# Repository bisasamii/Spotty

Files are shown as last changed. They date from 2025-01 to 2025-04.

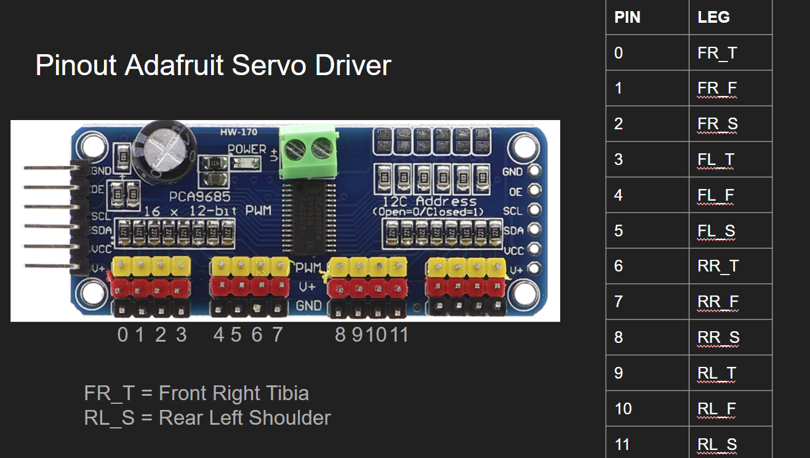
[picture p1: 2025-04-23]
Electronics/Wiring Diagrams/Servo Controller Pinout.png

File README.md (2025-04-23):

# Spotty
A quadruped Robot Dog based on the Boston Dynamics Spot
This repository contains all documentation, CAD files, electronic schematics.

<p align="center">
  Spotty Robot 1
  Spotty Robot 2
</p>

## Project Overview

Spotty is a four-legged (quadruped) open-source robot designed as a low-threshold learning platform for young talents interested in robotics and quantum technologies. The robot is constructed from PLA and can be extended with various modules, including a low-cost NV-based quantum sensor. The project aims to inspire curiosity and provide practical access to complex technologies.

Key features:
- Modular quadruped design inspired by Boston Dynamics' Spot
- Controlled by a Teensy 4.1 microcontroller with Adafruit PCA9685 for servo control
- 3D-printed components
- Integration of a basic NV-center quantum sensor (fluorescence-based magnetometer)
- Open-source hardware and software for educational purposes

## Repository Contents

- `/CAD`: 3D models (STL) for robot parts
- `/Electronics`: Schematics, wiring diagrams, and bill of materials
- `/Code`: Arduino/Teensy code for robot and remote
- `/Docs`: Detailed documentation

## Getting Started

1. Print the necessary parts using FDM 3D printing (recommended material: PLA).
2. Assemble the mechanical components and electronics following the guides in `/Docs`.
3. Upload the code from `/Code` to your MCUs.
4. Explore and extend Spotty!

## Requirements

- Electronics from bill of materials
- Basic tools for 3D printing and electronics assembly

## Acknowledgements

- Inspired by the SpotMicro Open Source Community

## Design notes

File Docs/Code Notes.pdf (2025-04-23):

## A couple of comments about the Code

1. Ensure that you have all libraries installed to run the code
2. If you have multiple SDA/SCL connected make sure to check the respective libraries for support. For example if you use the pins SDA1 and SCL1 you have to use “Wire1” in the arduino code. Not every library supports Wire1, Wire2,...
So you will have to make changes to the library to get everything to work

How the code is built:
The code has a main .ino file which is basically the main program. I have added multiple header files to make everything more clean:
- globals: Here are some global variables, constants an macros that you can change to your needs (for example servo settings, measurements,...)
- functions: Here are some functions for my mp3 module, NRF and compass module. Basically everything that is not related to servos or movement
- myBody: For the servos and movement of the robot I have decided to do a object oriented approach. The “MyBody” class controls the entire robot body, coordinates leg movements, selects the gait type, and regulates the walking behavior.
- myLeg: Declares the MyLeg class, which represents a single robot leg. It includes methods for stepping, position control, and updating the servos at the joints.
- myServoMotor: Declares the ServoMotor class, which encapsulates control of a servo motor, including motion interpolation, limits, correction factors, and direct actuation of the motor.

How the code generally works:
To understand how the code operates generally it is important to understand how the main .ino file operates. This picture can help you with this:

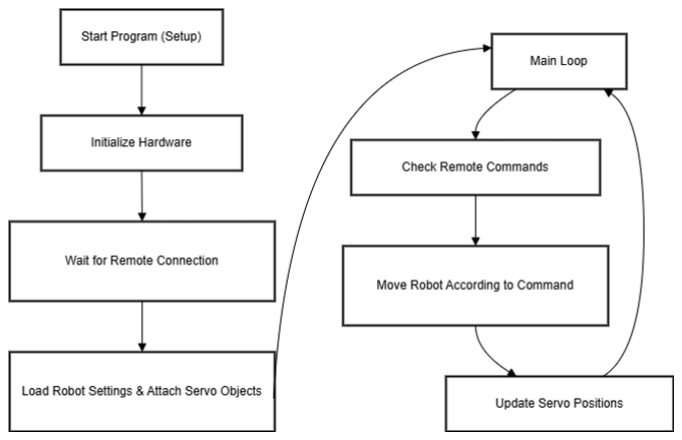
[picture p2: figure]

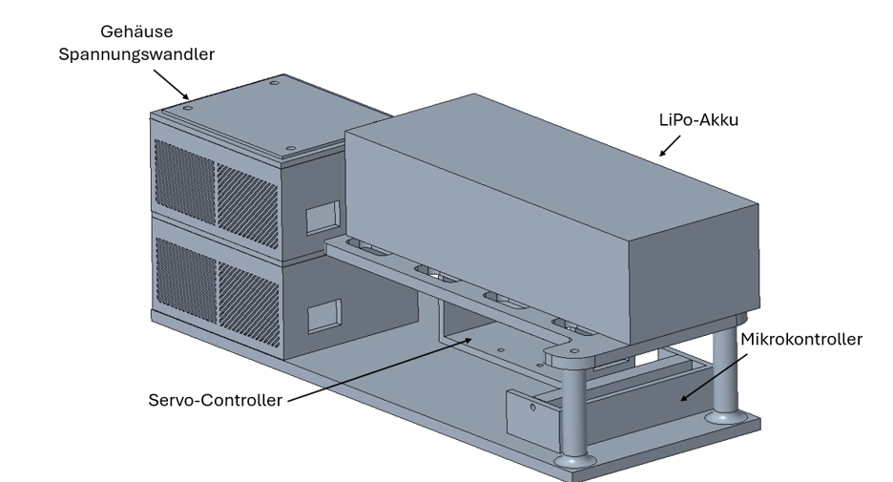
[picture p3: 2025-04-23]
Docs/Electronics Bracket.png

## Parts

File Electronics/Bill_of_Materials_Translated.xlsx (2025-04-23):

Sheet: Spotty
Name | Description | Quantity | Example Link
Motor (35kgcm) | Feetech FT6335 | 12 | https://www.premium-modellbau.de/feetech-ft6335-digital-metall-servo-67g-35kg-0-192sec-6v-8-4v-robotik-3600
Servo Controller | PCA9685 16 Channel 12 Bit PWM | 1 | https://www.amazon.de/AZDelivery-PCA9685-Servotreiber-Arduino-Raspberry/dp/B072N8G7Y9?hvadid=697141436093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
Microcontroller | Teensy 4.1 (much faster!) | 1 | https://www.amazon.de/Teensy-4-1-Mit-Stiftleisten/dp/B08CTM3279?__mk_de_DE=%C3%85M%C3%85%C5%BD%C3%95%C3%91
Servo Extensions | 3-pin Extension Cable for Servo Motors | 12 | https://www.amazon.de/Verl%C3%A4ngerungskabel%EF%BC%8CJR-Servoverl%C3%A4ngerung%EF%BC%8CServokabel%EF%BC%8CServokabel-Stecker-Verl%C3%A4ngerung%EF%BC%8C-sizes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
Step-Down Converter | 12 A output, converts battery voltage to 8.4V for servos | 1 | https://www.amazon.de/AZDelivery-Spannungsregler-Spannungswandler-Einstellbar-kompatibel/dp/B08T12J8KL
Step-Down Converter | Converts to Arduino logic voltage | 1 | https://www.amazon.de/Converter-Binghe-Spannungsregler-Einstellbares-Abw%C3%A4rtsmodul/dp/B0D7BWSTCX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
On/Off Power Switch | Must be suitable for high current | 1 | https://www.amazon.de/Demeras-Hochstrom-EIN-Aus-Schalter-RC-Flugzeugmodell-Schaltersteuerungssystem/dp/B08SLXX1J2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
Motor On/Off Switch | 12V | 1 | https://www.amazon.de/Kippschalter-Schalter-Wasserdicht-Wippschalter-Beleuchtet/dp/B0CQVKPJ39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
PowerTrain Cable, Red | For wiring before the voltage converter | 1 | https://www.amazon.de/Makerfire-Silikondraht-Elektrokabel-Kupfer-Hochtemperaturdraht-Flugzeugbatterien/dp/B09NFGJHYJ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
PowerTrain Cable, Black | For wiring before the voltage converter | 1
Low Voltage Cable | For logic boards (e.g., Arduino) | 1 | https://www.amazon.de/75mm%C2%B2Silikon-Elektronik-Elektrischer-RC-Flugzeuge-Haushaltsger%C3%A4te/dp/B09GKB582P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
DC Voltmeter Set | Monitor PowerTrain voltage | 1 | https://www.amazon.de/GTIWUNG-Spannungspr%C3%BCfer-Led-anzeige-Verpolungsschutz-Druckmessung/dp/B0BWLS9MVX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
Servo Tester | Calibrate the servos | 1 | https://www.amazon.de/diymore-Digital-Aluminiumgeh%C3%A4use-Multifunktions-Servocontroller/dp/B09Y94LLP6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
Battery Holder | For servo tester | 1 | https://www.amazon.de/VGOL-Batteriehalter-Empf%C3%A4ngergeh%C3%A4use-AA-Batterieeins%C3%A4tze-JST-Stecker/dp/B09QHRLMPX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
Servo Horn Set | Aluminium Buttons | 1 | https://www.amazon.de/DollaTek-Aluminium-Metall-H%C3%B6rner-Roboter/dp/B07F71J1Q2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
Screw & Nut Set | M2, M3, M4, M5 | 1 | https://www.amazon.de/Schrauben-Zylinderschrauben-Innensechskant-Unterlegscheiben-Gewindeschrauben/dp/B0CZNRW4MJ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
Bearing Set | 8165mm | 1 | https://www.amazon.de/ANGEEK-Kugellager-Metallkugellager-Doppelschild-Rillenkugellager/dp/B08Z8H3SV5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
Threaded Inserts Set | M2,M3,M4,M5 | 1 | https://www.amazon.de/ruthex-Gewindeeinsatz-Sortimentskasten-St%C3%BCck-Kunststoffteile/dp/B08K1BVGN9
Battery Pack | 14.8V 5000mAh | 1

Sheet: Remote
Name | Description | Quantity | Example Link
OLED 1 | Small Screen | 1 | https://www.amazon.de/MakerHawk-Anzeigemodul-Bildschirm-kompatibel-Mikrocontollern/dp/B07BDFXFRK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
OLED 2 | Large Screen | 1 | https://www.amazon.de/gp/product/B0CFFK32S8/ref=sw_img_1?smid=AE3E5WPQSSR6E&th=1
Joystick Module |  | 2 | https://www.amazon.de/gp/product/B077Z8QN3S/ref=sw_img_1?smid=A1XDN6LSMACAXM&psc=1
Trigger Switch |  | 4 | https://www.amazon.de/gp/product/B07VCCNVZP/ref=sw_img_1?smid=A8Q1GF4RT2D75&th=1
Sliding Potentiometer |  | 4 | https://www.amazon.de/gp/product/B07WSQPJ79/ref=sw_img_1?smid=AQ1IBDB6G2RRD&psc=1
Momentary Push Button | Mode Switch | 2 | https://www.amazon.de/gp/product/B0DFMMG1ZP/ref=sw_img_1?smid=A1GIQVBLUITC0P&th=1
LED | for indicator | 1 | https://www.amazon.de/gp/product/B088K8DVMQ/ref=sw_img_1?smid=A29559WHI6ZTR8&th=1
Battery + Charging Cable |  | 1 | https://www.amazon.de/gp/product/B08YJQDRSM/ref=sw_img_1?smid=A1CTK3ECWVKPGM&psc=1
3-Pole On/Off Switch |  | 1 | https://www.amazon.de/gp/product/B0CSCZGR68/ref=sw_img_1?smid=A1GIQVBLUITC0P&psc=1
3.3 V Regulator |  | 1 | https://www.amazon.de/gp/product/B07VGNPP7N/ref=sw_img_1?smid=A1X7QLRQH87QA3&th=1
5 V Regulator |  | 1 | https://www.amazon.de/gp/product/B07DJ5HZ7G/ref=sw_img_1?smid=A3SCFTIO8CSK1X&psc=1
NRF24 |  | 2

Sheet: Remote2
Name | Description | Quantity | Example Link
Joystick Module |  | 2 | https://www.amazon.de/gp/product/B077Z8QN3S/ref=sw_img_1?smid=A1XDN6LSMACAXM&psc=1
LED |  | 1
Battery + Charging Cable |  | 1 | https://www.amazon.de/gp/product/B08YJQDRSM/ref=sw_img_1?smid=A1CTK3ECWVKPGM&psc=1
5V Regulator |  | 1 | https://www.amazon.de/gp/product/B07DJ5HZ7G/ref=sw_img_1?smid=A3SCFTIO8CSK1X&psc=1
NRF24 |  | 2

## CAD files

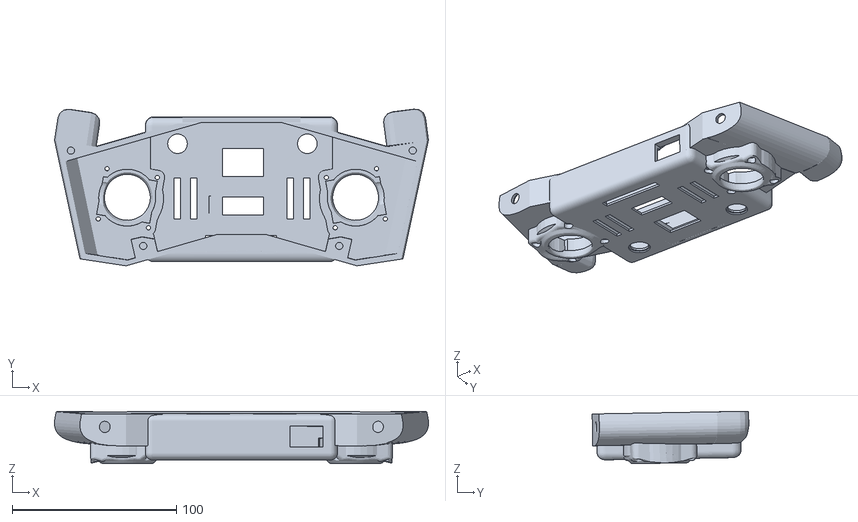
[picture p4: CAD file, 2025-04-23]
CAD/Remote/Cover_Front_V2.stl
227.6 x 95.3 x 31.9

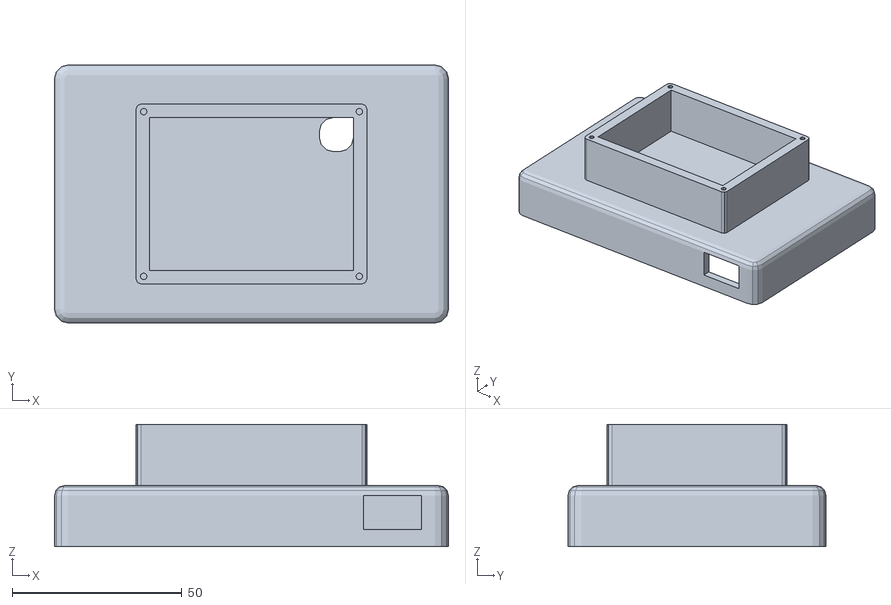
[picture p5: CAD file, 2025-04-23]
CAD/Remote2/Back.stl
116.0 x 76.0 x 36.0

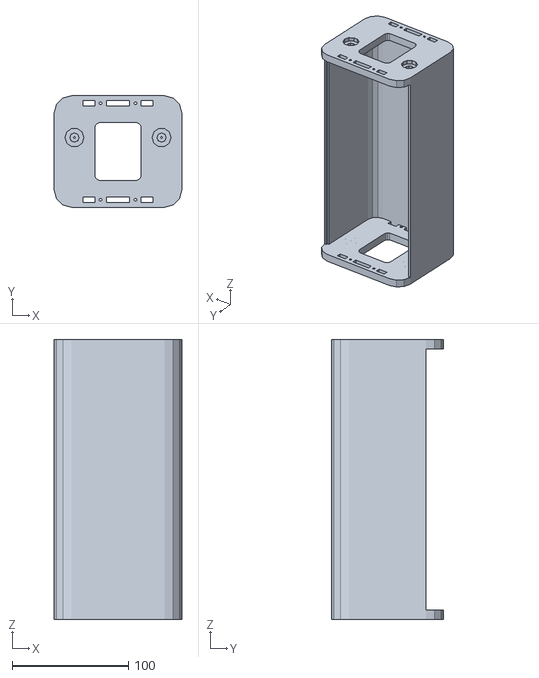
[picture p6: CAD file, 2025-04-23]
CAD/Spotty/Body/BODY_SPOTTY.stl
110.0 x 96.0 x 241.0

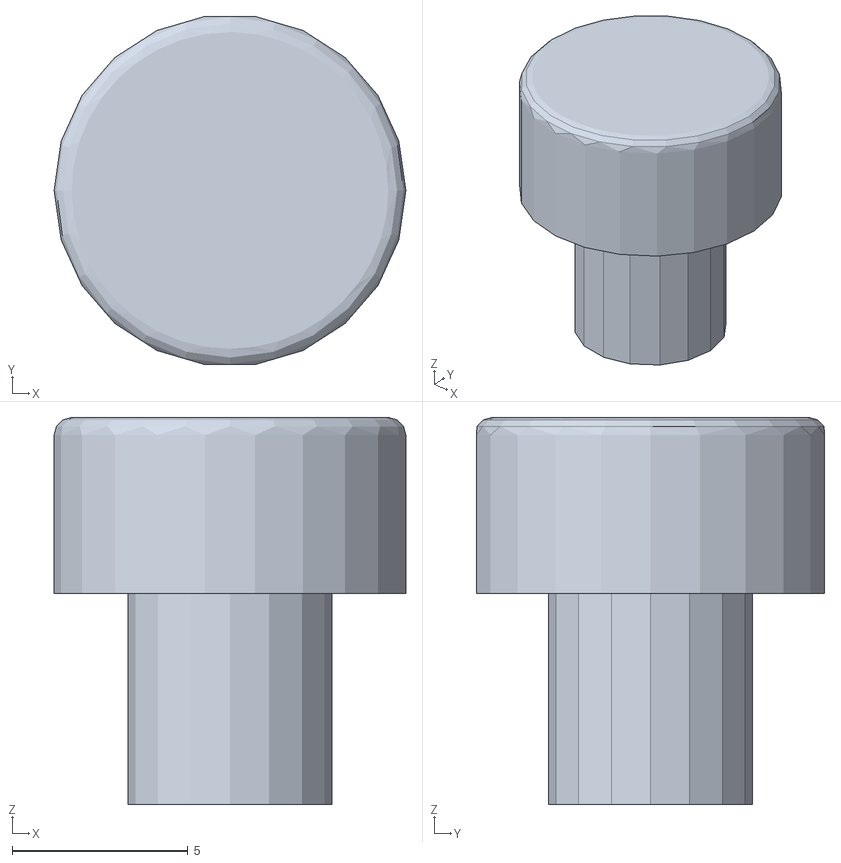
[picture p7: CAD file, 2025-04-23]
CAD/Spotty/Body/Lock/lock3.stl
10.0 x 9.90 x 11.0

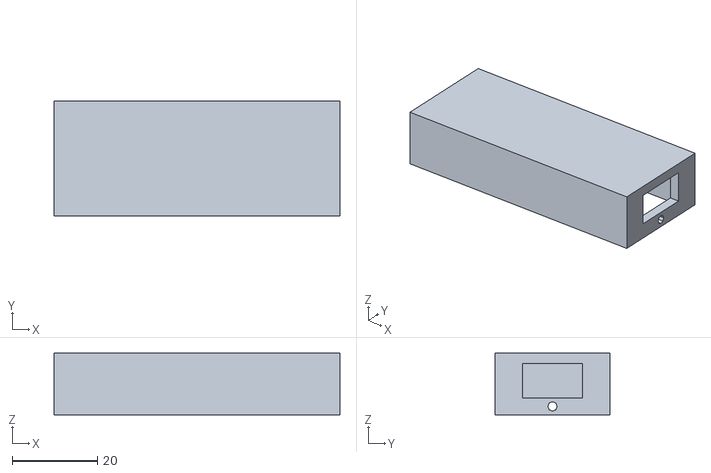
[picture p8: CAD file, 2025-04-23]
CAD/Spotty/Electronicsbracket/teensy_case.stl
67.0 x 27.0 x 14.5

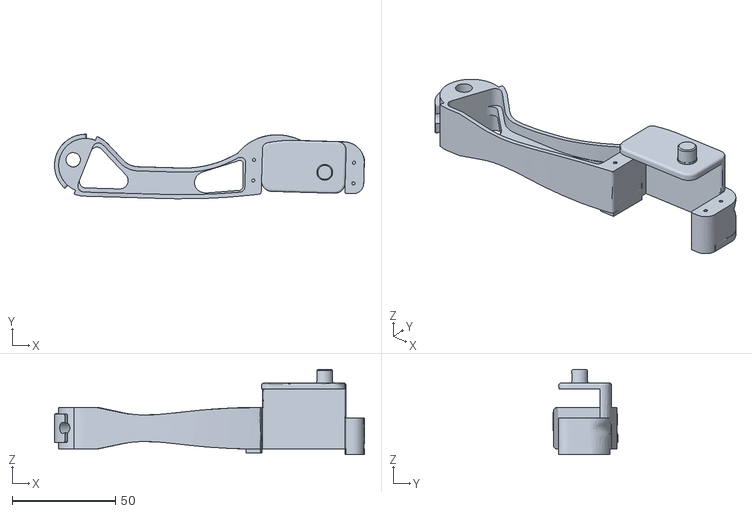
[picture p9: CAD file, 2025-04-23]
CAD/Spotty/Leg/TIBIA_RIGHT_SPOTTY.stl
150.2 x 31.3 x 41.2

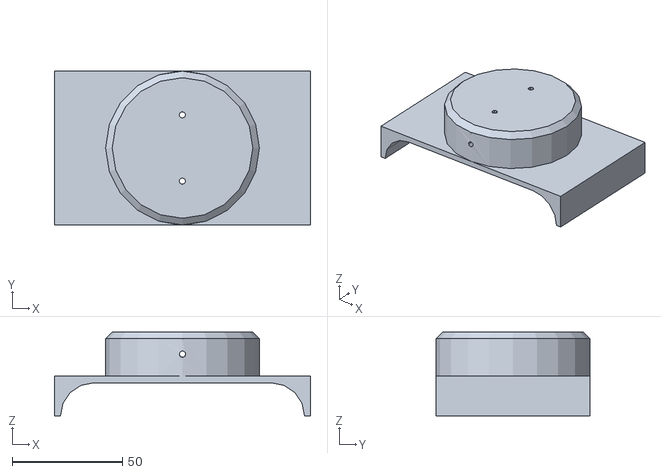
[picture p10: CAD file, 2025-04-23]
CAD/Spotty/Stand/aufnahme.stl
116.0 x 69.7 x 38.0

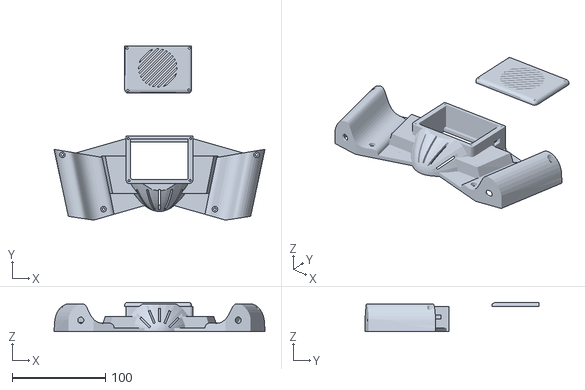
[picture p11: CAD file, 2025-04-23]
CAD/Remote/Cover_Back_V2.stl
225.8 x 186.5 x 31.1

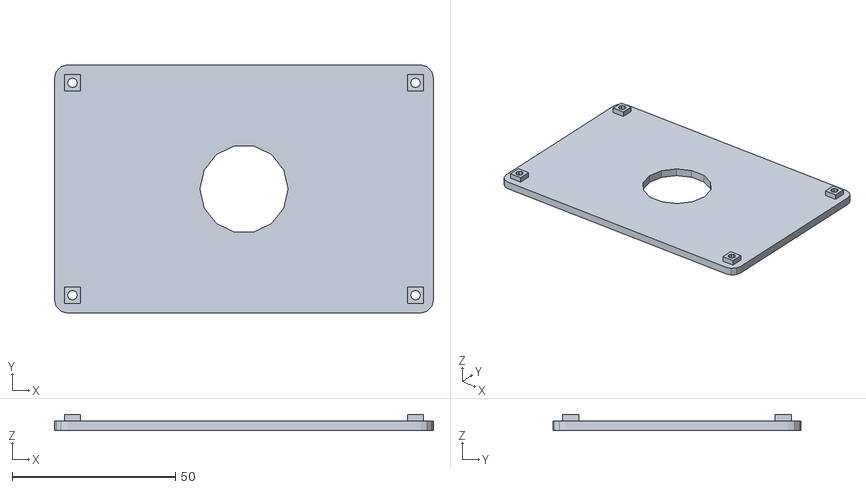
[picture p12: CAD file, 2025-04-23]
CAD/Remote2/Front.stl
116.0 x 76.0 x 5.00

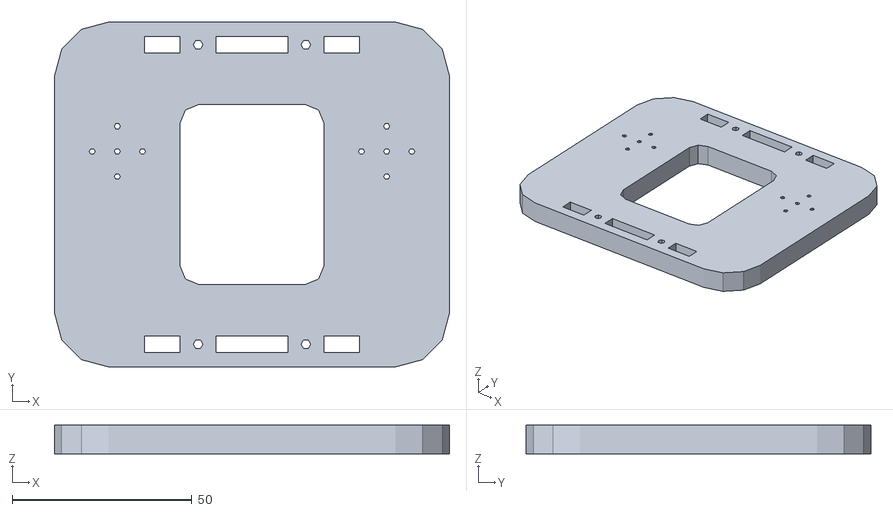
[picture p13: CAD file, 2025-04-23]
CAD/Spotty/Body/FACEPLATE2_SPOTTY.stl
110.0 x 96.0 x 8.00

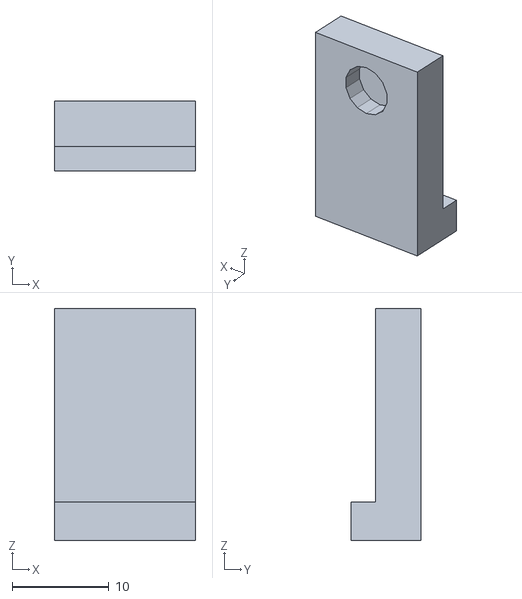
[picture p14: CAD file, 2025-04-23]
CAD/Spotty/Body/Lock/lock2.stl
14.6 x 7.20 x 24.0

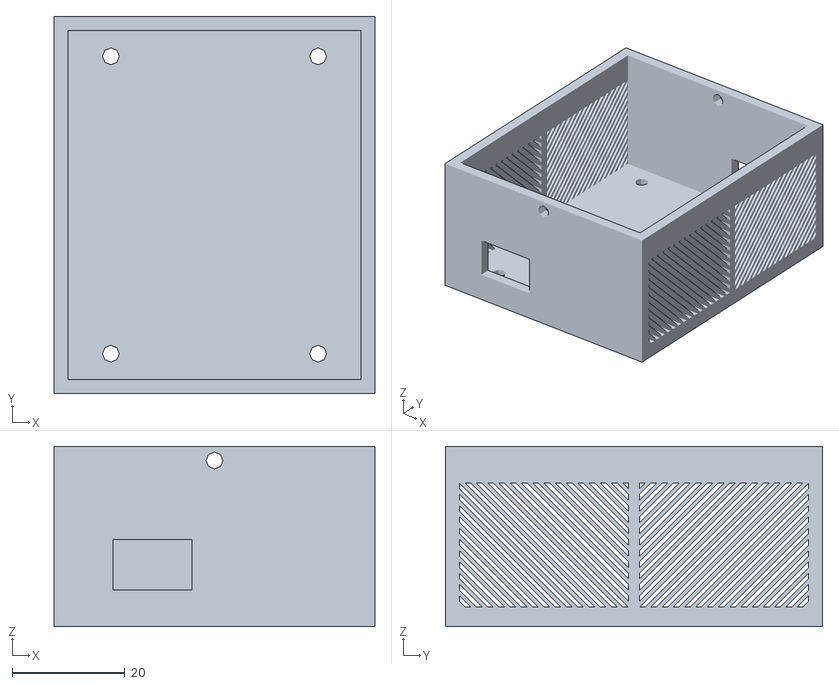
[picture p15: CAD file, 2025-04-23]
CAD/Spotty/Electronicsbracket/BUCK_CONVERTER_CASE.stl
57.0 x 67.0 x 32.0

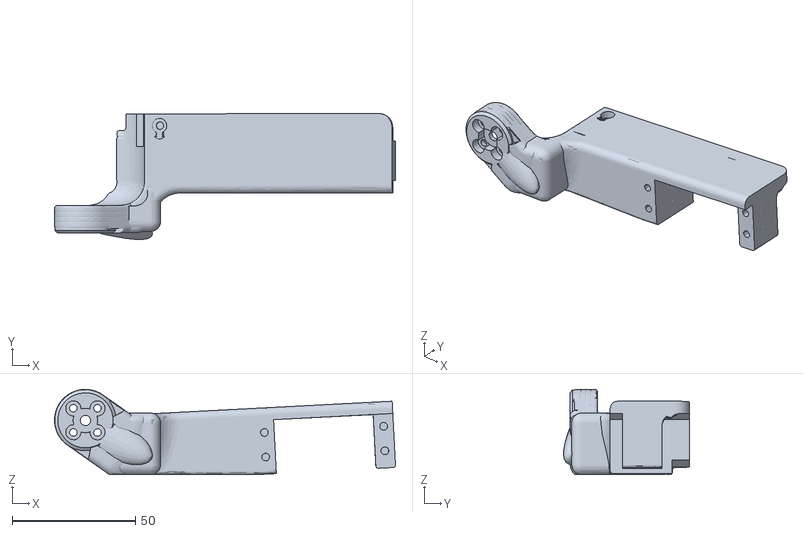
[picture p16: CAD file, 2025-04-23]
CAD/Spotty/Leg/FEMUR_RIGHT_SPOTTY.stl
138.5 x 51.2 x 34.7

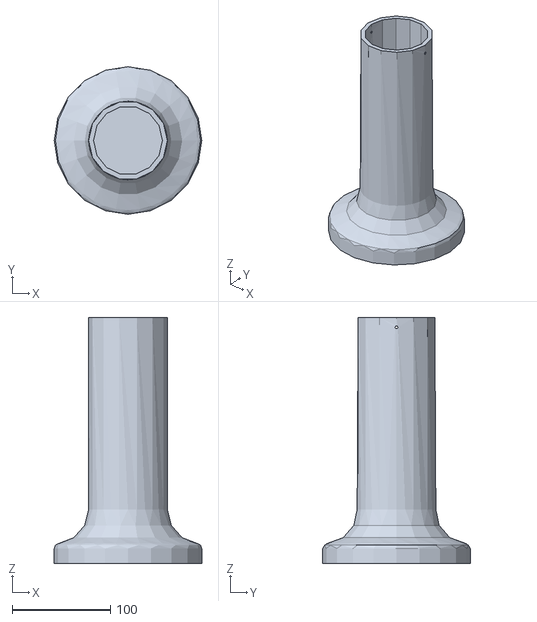
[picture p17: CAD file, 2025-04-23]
CAD/Spotty/Stand/base.stl
150.0 x 150.0 x 250.0

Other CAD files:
CAD/Remote2/Batterylid.stl
CAD/Spotty/Body/BODYLID_SPOTTY.stl
CAD/Spotty/Body/Lock/lock1.stl
CAD/Spotty/Electronicsbracket/servo_board_case.stl
CAD/Spotty/Body/CONNECTORBODY_SPOTTY.stl
CAD/Spotty/Body/FACEPLATE_SPOTTY.stl
CAD/Spotty/Electronicsbracket/baseplate.stl
CAD/Spotty/Electronicsbracket/buck_converter_lid.stl
CAD/Spotty/Electronicsbracket/teensy_lid.stl
CAD/Spotty/Electronicsbracket/upper_plate.stl
CAD/Spotty/Leg/BRACE_SPOTTY.stl
CAD/Spotty/Leg/COAX_RIGHT_SPOTTY.stl
CAD/Spotty/Leg/FEMURCOVER_RIGHT_SPOTTY.stl

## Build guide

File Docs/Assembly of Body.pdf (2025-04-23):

## Assembly of the Body

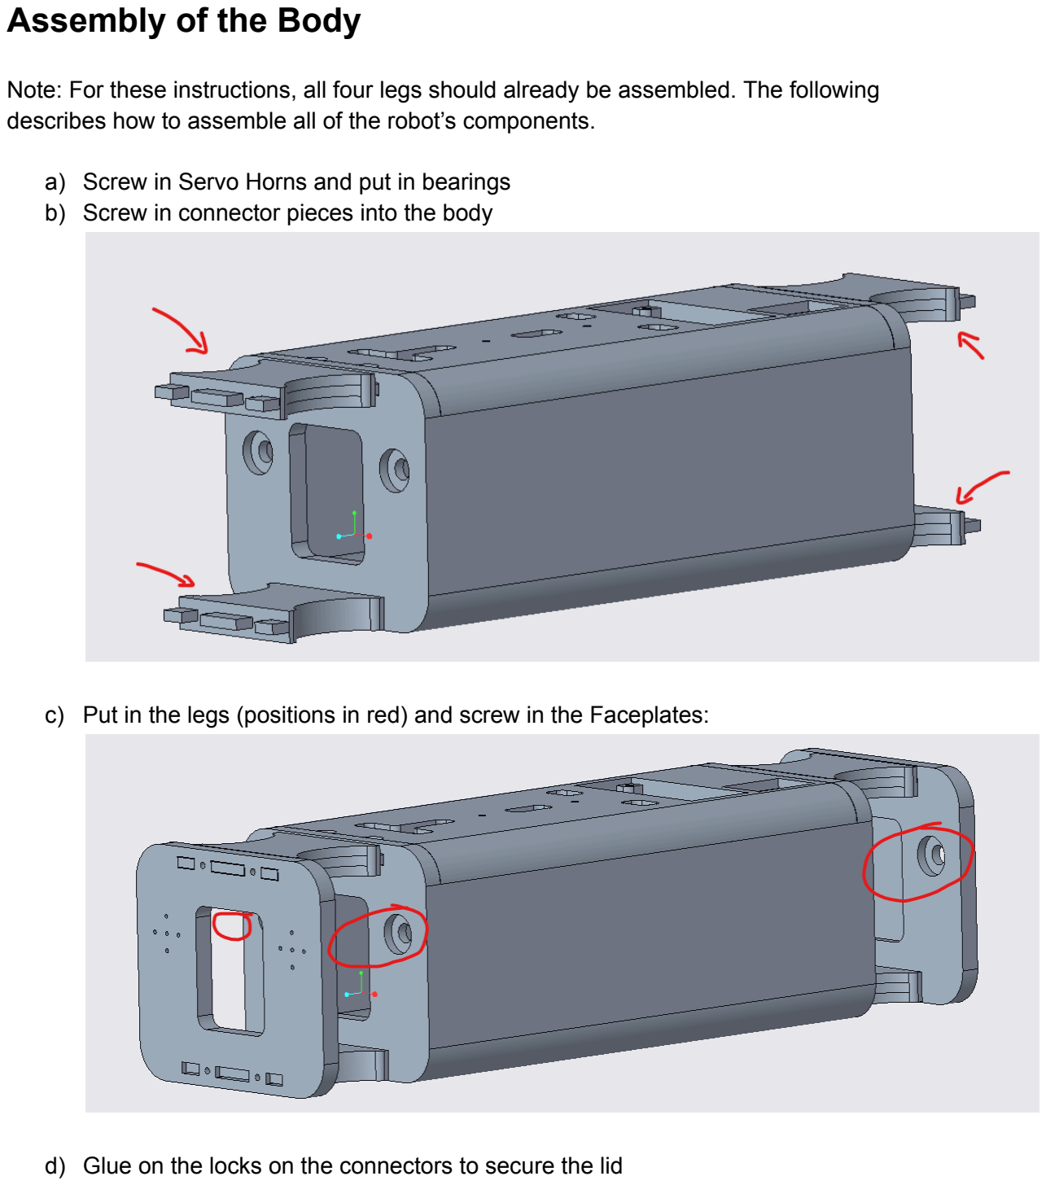
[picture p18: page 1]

Note: For these instructions, all four legs should already be assembled. The following describes how to assemble all of the robot’s components.

a) Screw in Servo Horns and put in bearings
b) Screw in connector pieces into the body
c) Put in the legs (positions in red) and screw in the Faceplates:
d) Glue on the locks on the connectors to secure the lid

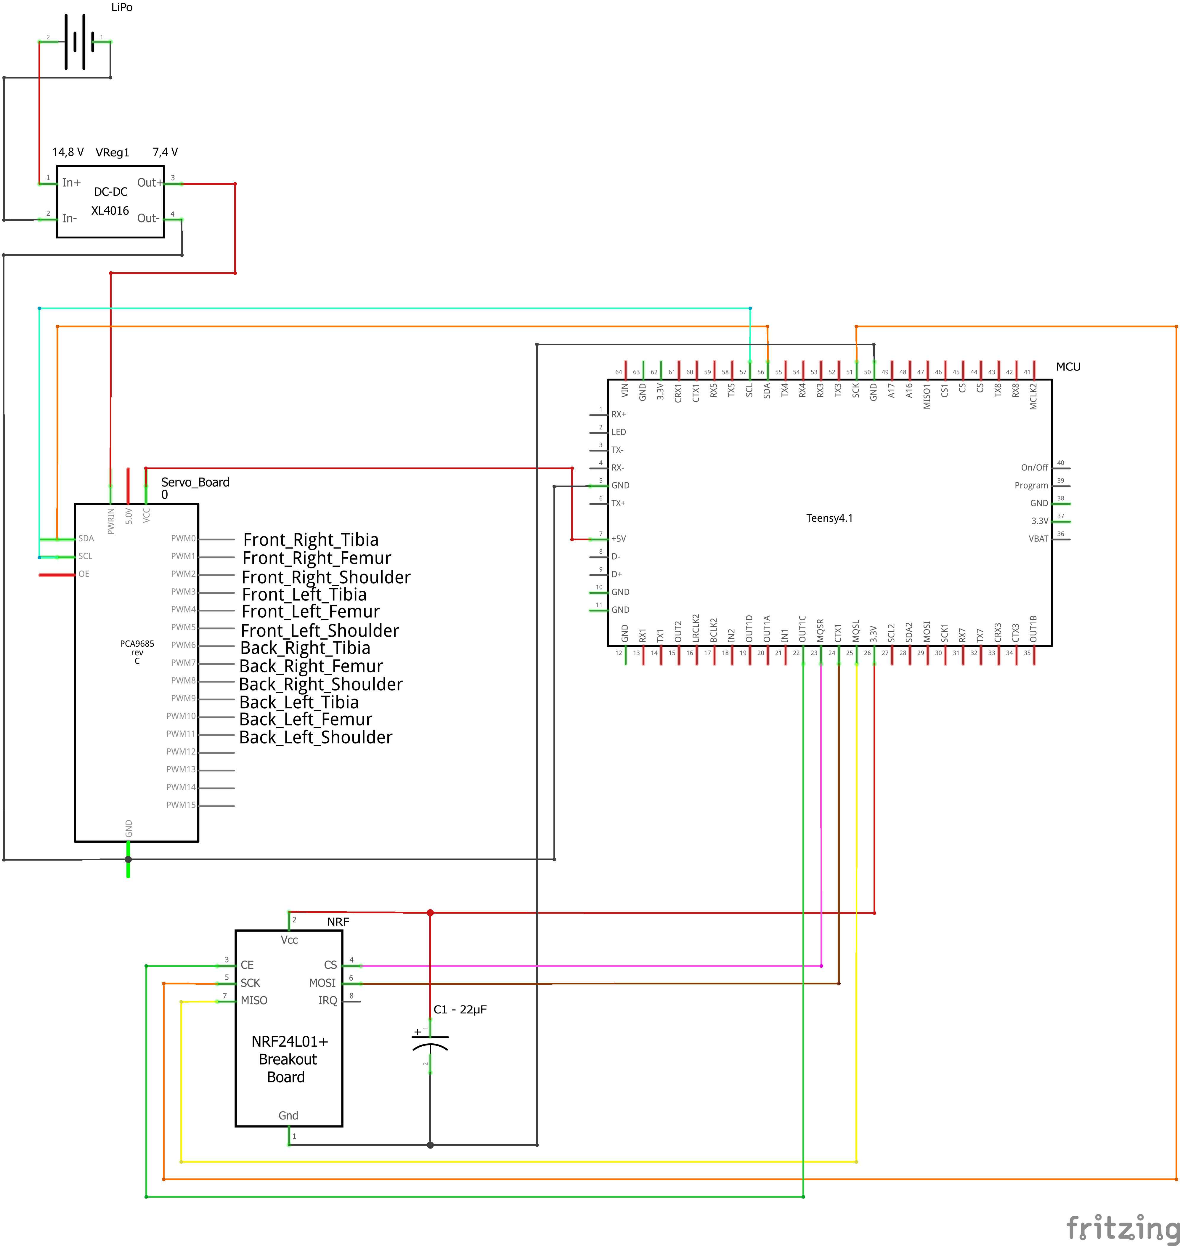
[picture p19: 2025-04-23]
Electronics/Wiring Diagrams/Spotty_Wiring.png

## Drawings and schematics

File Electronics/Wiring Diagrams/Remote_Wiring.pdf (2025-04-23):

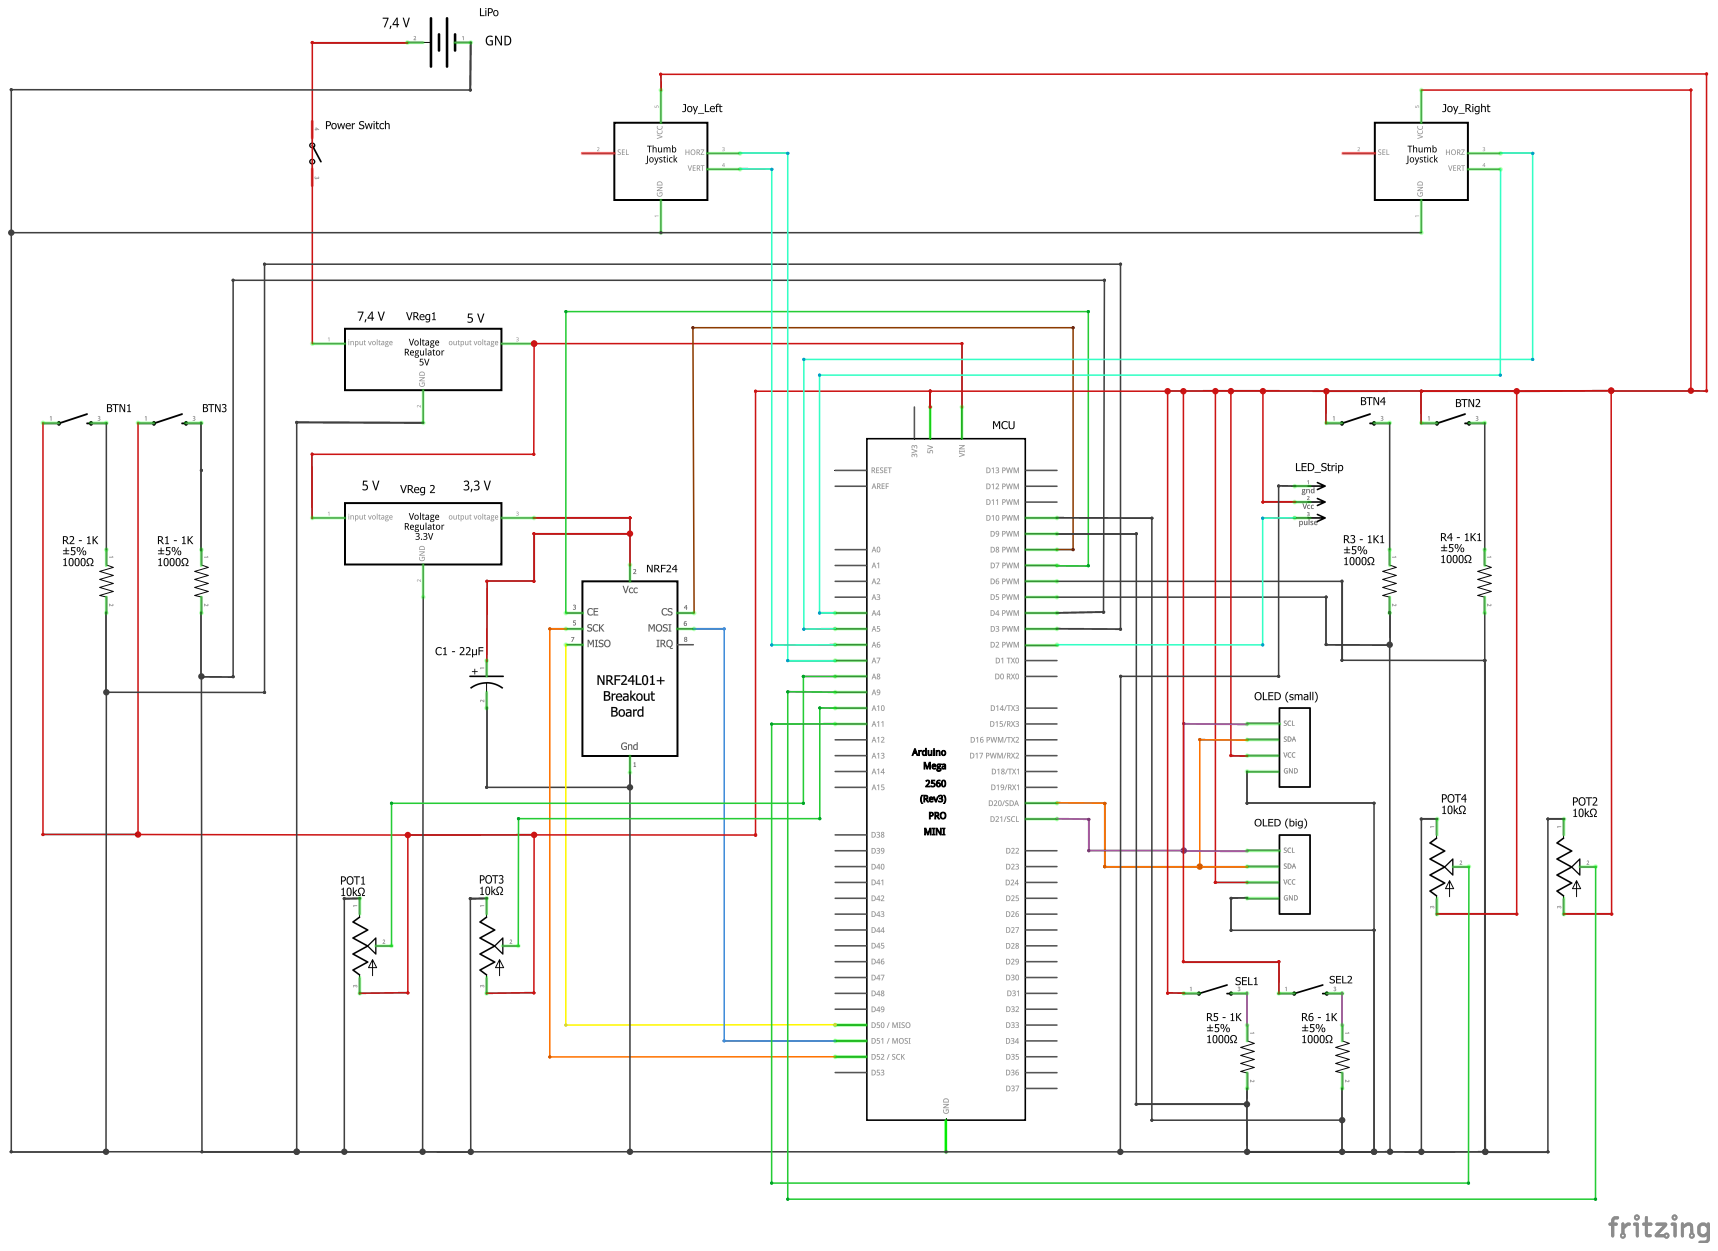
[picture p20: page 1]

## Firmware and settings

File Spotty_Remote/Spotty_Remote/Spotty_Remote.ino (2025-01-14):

#include "globals.h"

//========================================
//  NRF24 Pin Wiring for Arduino Mega/Nano:
//  pin 7/7 -> CE pin
//  pin 8/8 -> CSN pin
//  pin 52/13 -> SCK pin
//  pin 51/11 -> MOSI pin
//  pin 50/12 -> MISO pin
//  pin xx -> IRQ pin (unused)
//========================================
//function prototypes
void fade(int redStartValue, int redEndValue, int greenStartValue, int greenEndValue, int blueStartValue, int blueEndValue, int totalSteps, int fadeBack, int rgbNum = 99);
void blink_rgb_num(int rgb_val[3], int rgb_val2[3], int rgbNum=99);


void setup() {
  Serial.begin(19200);
  while (!Serial) {
  }

  delay(3000);
  if (nrf_active) {
    if (!radio.begin()) {
      if (debug2) Serial.println(F("radio hardware is not responding!!"));
      while (1) {}
    } else {
      if (debug2) Serial.println(F("radio hardware is ready!"));
      radio.setPALevel(RF24_PA_LOW);
      radio.setPayloadSize(sizeof(tm_data));
      radio.setChannel(124);
      radio.openWritingPipe(address);
      radio.enableAckPayload();
      radio.setRetries(5,5); // delay, count

      if (debug2) Serial.println(F("radio ready to transmit"));
    }
  }

  pinMode(POT1_PIN, INPUT);
  pinMode(POT2_PIN, INPUT);
  pinMode(POT3_PIN, INPUT);
  pinMode(POT4_PIN, INPUT);

  pinMode(LJX_PIN, INPUT);
  pinMode(LJY_PIN, INPUT);

  pinMode(RJX_PIN, INPUT);
  pinMode(RJY_PIN, INPUT);

  led_strip.begin();
  led_strip.setBrightness(rgb_bright);
  wipe_strip();

  pinMode(BTN1_PIN, INPUT_PULLUP);
  pinMode(BTN2_PIN, INPUT_PULLUP);
  pinMode(BTN3_PIN, INPUT_PULLUP);
  pinMode(BTN4_PIN, INPUT_PULLUP);

  pinMode(SEL1_PIN, INPUT_PULLUP);
  pinMode(SEL2_PIN, INPUT_PULLUP);
  
  // initialize with the I2C addr
  display.begin(SSD1306_SWITCHCAPVCC, OLED_ADDR);  
  display2.begin(SSD1306_SWITCHCAPVCC, OLED_ADDR2);  

  rgb_check(8);
  
  display.clearDisplay();
  display.setTextSize(1);
  display.setTextColor(WHITE);
  display.setCursor(0,0);
  display.println("Initializing...");
  display.display();
    
  display2.clearDisplay();
  display2.setTextSize(1);
  display2.setTextColor(WHITE);
  display2.setCursor(10,0);
  display2.println("Initializing...");
  display2.display();
  
  delay(2000);
  display.clearDisplay();
  display2.clearDisplay();
  display2.setTextSize(2);
  
  //animate bitmap
  display.drawBitmap(-10, 5,  smbmp, 128, 64, WHITE);
  display.display();
  display.startscrollright(0x00, 0x07);

  //strobe version banner
  for (int i=25;i>0;i--) {
    int d = (i*4);
    if (i > 22) d = (i*10);
    if (i == 25) d = (i*100);
    display2.setCursor(22, 2);
    display2.setTextSize(2);
    display2.println("SPOTTY");
    display2.setCursor(16, 18);
    display2.print("REMOTE");
    display2.setCursor(86, 22);
    display2.setTextSize(1);
    display2.print(" v");
    display2.println(VERSION);
    display2.display();
    delay(d);
    display2.clearDisplay();
    display2.display();
    if (i == 25) d = (i*10);
    delay(d);
  }
  display2.clearDisplay();
  display2.display();
  delay(2000);

  display2.setCursor(30,12);
  display2.setTextSize(3);
  display2.print("READY!");
  display2.display();

  display.stopscroll();
  display.clearDisplay();
  display.display();

  //init remote with Nova
  if (nrf_active) {
    for (int i = 0; i < data_num; i++) {
      tm_data[i] = 0;
    }
    tm_resp = nrf_check();
  }

  if (debug) Serial.println(F("Ready!"));
  pattern = 10;
  pattern_cnt = 16;
  pattern_int = 150;
}

void loop() {
  if (millis() - controlsUpdate > controlsInterval) {
    check_pots();
    check_buttons();
    check_joysticks();
    check_mode();
  }

  if (nrf_active && (millis() - lastNRFUpdate > nrfInterval)) tm_resp = nrf_check();

  if (millis() - lastRGBUpdate > rgbInterval) rgb_check(pattern);
  if (millis() - lastOLEDUpdate > oledInterval) oled_refresh();
  if (millis() - lastOLED2Update > oled2Interval) oled2_refresh();
  if (millis() - lastDisplayUpdate > displayInterval) update_display(2);

  if (batt_active && (millis() - lastBatteryUpdate > batteryInterval)) battery_check(0); 
  if (activity_active && millis() - inactivityUpdate > inactivityInterval) inactivity_check(); 

  if (debug3) {

    Serial.print("pot1:");
    Serial.print(p1);
    Serial.print("\tpot2:");
    Serial.print(p2);
    Serial.print("\tpot3:");
    Serial.print(p3);
    Serial.print("\tpot4:");
    Serial.print(p4);
  
    if (!plotter) {
      Serial.print("\tbtn1:");
      Serial.print(b1);
      Serial.print("\tbtn2:");
      Serial.print(b2);
      Serial.print("\tbtn3:");
      Serial.print(b3);
      Serial.print("\tbtn4:");
      Serial.print(b4);
  
      Serial.print("\tsel1:");
      Serial.print(s1);
      Serial.print("\tsel2:");
      Serial.print(s2);
      Serial.print("\tsel3:");
      Serial.print(s3);
    }
  
    Serial.print("\trjx:");
    Serial.print(analogRead(RJX_PIN));
    Serial.print("\trjy:");
    Serial.print(analogRead(RJY_PIN));
  
    Serial.print("\tljx:");
    Serial.print(analogRead(LJX_PIN));
    Serial.print("\tljy:");
    Serial.println(analogRead(LJY_PIN));
    delay(50);
  }

}

bool nrf_check() {
  bool resp = false;

  if (tm_data) {
    resp = radio.write(&tm_data, sizeof(tm_data));
    if (resp) {
      if (radio.isAckPayloadAvailable()) {
        radio.read(&rc_data, sizeof(rc_data));
        if (debug2) {
          for (int i = 0; i < data_num; i++) {
            Serial.print(rc_data[i]);Serial.print("\t");
          }
          Serial.println(" ACK REC");
        }
      }

      if (debug2) {
        for (int i = 0; i < data_num; i++) {
          Serial.print(tm_data[i]);Serial.print("\t");
        }
        Serial.println(" DATA SENT");
      }
    } else {
      //handle failed transmission
      if (debug2) {
        Serial.print(F("Transmission failed! "));
        Serial.println(" ");
      }
    }

    lastNRFUpdate = millis();
  }

  return resp;
}

void inactivity_check() {
  if (inactivity_set) {
    inactivity_cnt++;
    if (debug) {
      Serial.print(F("icnt: "));
      Serial.println(inactivity_cnt);
    }

    //put into sleep mode
    if (inactivity_cnt == inactivity_loop) {
      if (debug) {
        Serial.println(F("update display"));
      }
      update_display(4);
    } else if (inactivity_cnt == (inactivity_loop * 2)) {
      inactivity_cnt = 0;
      display.clearDisplay();
      display2.clearDisplay();
    }
  } else {
    inactivity_cnt = 0;
  }
  inactivity_set = 1;
  inactivityUpdate = millis();
}

void check_pots() {
  int updis = 0;
  if (debug4) {
    pot_max = 128;    //adjust max to OLED pixel width for debug mode
  }

  int p1c = analogRead(POT1_PIN);
  if (p1c != p1p) {
    //double-check jumpy pots
    if (p1c == analogRead(POT1_PIN)) {
      p1 = map(p1c, 0, 1023, pot_max, pot_min);
      if (p1 > pot_slack) {
        if (p1c > (p1p + pot_slack) || p1c < (p1p - pot_slack)) {
          inactivity_set = 0;
        }
        p1p = p1c;
        tm_data[6] = p1;
  
        if (debug4) {
          bdrawline(2,1,1,128,1);
          wdrawline(2,1,1,p1,1);
    
          cur_rgb_val1[0] = 125; cur_rgb_val1[1] = 0; cur_rgb_val1[2] = 125;
          cur_rgb_val2[0] = 0; cur_rgb_val2[1] = 125; cur_rgb_val2[2] = 125;
          rgb_num = 0;
          if (p1 > 100) {
            rgb_num = 4;
          } else if (p1 > 75) {
            rgb_num = 3;
          } else if (p1 > 50) {
            rgb_num = 2;
          } else if (p1 > 25) {
            rgb_num = 1;
          }
          pattern = 9;
          pattern_cnt = 1;
          pattern_int = 10;
        } else {
          per1 = map(p1, pot_max, pot_min, 100, -100); // convert reading to a percentage
          if (per1 < 3 && per1 > -3) per1 = 0;
          if (per1 != pper1) {
            pper1 = per1;
            updis = 1;
          }
        }
      }
    }
  }

  int p2c = analogRead(POT2_PIN);
  if (p2c != p2p) {
    //double-check jumpy pots
    if (p2c == analogRead(POT2_PIN)) {
      p2 = map(p2c, 0, 1023, pot_max, pot_min);
      if (p2 > pot_slack) {
        if (p2c > (p2p + pot_slack) || p2c < (p2p - pot_slack)) {
          inactivity_set = 0;
        }
        p2p = p2c;
        tm_data[7] = p2;
  
        if (debug4) {
          bdrawline(2,1,5,128,5);
          wdrawline(2,1,5,p2,5);
    
          cur_rgb_val1[0] = 255; cur_rgb_val1[1] = 0; cur_rgb_val1[2] = 55;
          cur_rgb_val2[0] = 55; cur_rgb_val2[1] = 0; cur_rgb_val2[2] = 255;
          rgb_num = 0;
          if (p2 > 100) {
            rgb_num = 4;
          } else if (p2 > 75) {
            rgb_num = 3;
          } else if (p2 > 50) {
            rgb_num = 2;
          } else if (p2 > 25) {
            rgb_num = 1;
          }
          pattern = 9;
          pattern_cnt = 1;
          pattern_int = 10;    
        } else {
          per2 = map(p2, pot_max, pot_min, 100, -100); // convert reading to a percentage
          if (per2 < 3 && per2 > -3) per2 = 0;
          if (per2 != pper2) {
            pper2 = per2;
            updis = 1;
          }
        }
      }
    }
  }

  int p3c = analogRead(POT3_PIN);
  if (p3c != p3p) {
    //double-check jumpy pots
    if (p3c == analogRead(POT3_PIN)) {
      p3 = map(p3c, 0, 1023, pot_max, pot_min);
      if (p3 > pot_slack) {
        if (p3c > (p3p + pot_slack) || p3c < (p3p - pot_slack)) {
          inactivity_set = 0;
        }
        p3p = p3c;
        tm_data[8] = p3;
  
        if (debug4) {
          bdrawline(2,1,26,128,26);
          wdrawline(2,1,26,p3,26);
    
          cur_rgb_val1[0] = 55; cur_rgb_val1[1] = 255; cur_rgb_val1[2] = 55;
          cur_rgb_val2[0] = 55; cur_rgb_val2[1] = 55; cur_rgb_val2[2] = 255;
          rgb_num = 0;
          if (p3 > 100) {
            rgb_num = 4;
          } else if (p3 > 75) {
            rgb_num = 3;
          } else if (p3 > 50) {
            rgb_num = 2;
          } else if (p3 > 25) {
            rgb_num = 1;
          }
          pattern = 9;
          pattern_cnt = 1;
          pattern_int = 10;
        } else {
          per3 = map(p3, pot_max, pot_min, 100, -100); // convert reading to a percentage
          if (per3 < 3 && per3 > -3) per3 = 0;
          if (per3 != pper3) {
            pper3 = per3;
            updis = 1;
          }
        }
      }
    }
  }

  int p4c = analogRead(POT4_PIN);
  if (p4c != p4p) {
    //double-check jumpy pots
    if (p4c == analogRead(POT4_PIN)) {
      p4 = map(p4c, 0, 1023, pot_max, pot_min);
      if (p4 > pot_slack) {
        if (p4c > (p4p + pot_slack) || p4c < (p4p - pot_slack)) {
          inactivity_set = 0;
        }
        p4p = p4c;
        tm_data[9] = p4;
  
        if (debug4) {
          bdrawline(2,1,31,128,31);
          wdrawline(2,1,31,p4,31);
    
          cur_rgb_val1[0] = 255; cur_rgb_val1[1] = 55; cur_rgb_val1[2] = 55;
          cur_rgb_val2[0] = 255; cur_rgb_val2[1] = 55; cur_rgb_val2[2] = 255;
          rgb_num = 0;
          if (p4 > 100) {
            rgb_num = 4;
          } else if (p4 > 75) {
            rgb_num = 3;
          } else if (p4 > 50) {
            rgb_num = 2;
          } else if (p4 > 25) {
            rgb_num = 1;
          }
          pattern = 9;
          pattern_cnt = 1;
          pattern_int = 10;
        } else {
          per4 = map(p4, pot_max, pot_min, 100, -100); // convert reading to a percentage
          if (per4 < 3 && per4 > -3) per4 = 0;
          if (per4 != pper4) {
            pper4 = per4;
            updis = 1;
          }
        }
      }
    }
  }

//  if (updis) update_display(1);
}

void check_buttons() {
  int b1c = digitalRead(BTN1_PIN);
  if (b1c != b1p) {
    b1 = b1c;
    b1p = b1c;
    inactivity_set = 0;
    tm_data[0] = b1;

    if (b1) {
      led_strip.setPixelColor(0, led_strip.Color(125, 125, 0));
    } else {
      led_strip.setPixelColor(0, led_strip.Color(0, 0, 0));
    }
    led_strip.show();
    if (debug4) {
      if (b1) {
        wfillcircle(2,40,20,5);
      } else {
        bfillcircle(2,40,20,5);
      }
    }
  }

  int b2c = digitalRead(BTN2_PIN);
  if (b2c != b2p) {
    b2 = b2c;
    b2p = b2c;
    inactivity_set = 0;
    tm_data[1] = b2;

    if (b2) {
      led_strip.setPixelColor(4, led_strip.Color(125, 125, 0));
    } else {
      led_strip.setPixelColor(4, led_strip.Color(0, 0, 0));
    }
    led_strip.show();
    if (debug4) {
      if (b2) {
        wfillcircle(2,88,20,5);
      } else {
        bfillcircle(2,88,20,5);
      }
    }
  }

  int b3c = digitalRead(BTN3_PIN);
  if (b3c != b3p) {
    b3 = b3c;
    b3p = b3c;
    inactivity_set = 0;
    tm_data[2] = b3;

    if (b3) {
      led_strip.setPixelColor(1, led_strip.Color(125, 125, 0));
    } else {
      led_strip.setPixelColor(1, led_strip.Color(0, 0, 0));
    }
    led_strip.show();
    if (debug4) {
      if (b3) {
        wfillcircle(2,30,10,5);
      } else {
        bfillcircle(2,30,10,5);
      }
    }
  }

  int b4c = digitalRead(BTN4_PIN);
  if (b4c != b4p) {
    b4 = b4c;
    b4p = b4c;
    inactivity_set = 0;
    tm_data[3] = b4;

    if (b4) {
      led_strip.setPixelColor(3, led_strip.Color(125, 125, 0));
    } else {
      led_strip.setPixelColor(3, led_strip.Color(0, 0, 0));
    }
    led_strip.show();
    if (debug4) {
      if (b4) {
        wfillcircle(2,98,10,5);
      } else {
        bfillcircle(2,98,10,5);
      }
    }
  }


  int s1c = digitalRead(SEL1_PIN);
  if (s1c != s1p) {
    s1 = s1c;
    s1p = s1c;
    inactivity_set = 0;
    tm_data[4] = s1;

    if (debug4) {
      if (s1) {
        wfillcircle(2,32,15,10);
        led_strip.setPixelColor(2, led_strip.Color(0, 255, 0));
      } else {
        bfillcircle(2,32,15,10);
        led_strip.setPixelColor(2, led_strip.Color(0, 0, 0));
      }
      led_strip.show();
    } else {
      if (s1 == LOW) {
      // Cycle through modes: 1 -> 2 -> 3 -> 4 -> 1 -> ...
      mode_index++;
      if (mode_index > 4) {
        mode_index = 1;
      }

      cur_rgb_val1[0] = 0; cur_rgb_val1[1] = 255; cur_rgb_val1[2] = 0;
      cur_rgb_val2[0] = 0; cur_rgb_val2[1] = 0; cur_rgb_val2[2] = 0;
      rgb_num = 99;
      pattern = 9;
      pattern_cnt = 1;
      pattern_int = 10;
      update_display(3);
    }
    }
  }

  int s2c = digitalRead(SEL2_PIN);
  if (s2c != s2p) {
    s2 = s2c;
    s2p = s2c;
    inactivity_set = 0;
    tm_data[5] = s2;

    if (debug4) {
      if (s2) {
        wfillcircle(2,96,15,10);
        led_strip.setPixelColor(2, led_strip.Color(255, 0, 0));
      } else {
        bfillcircle(2,96,15,10);
        led_strip.setPixelColor(2, led_strip.Color(0, 0, 0));
      }
      led_strip.show();
    } else {
      
      if (s2 == LOW) {
      selected_mode = mode_index;
      display2.clearDisplay();
      display2.setCursor(0, 0);
      display2.setTextSize(2);
      switch (mode_index) {
        case 1:
          display2.print("Walk");
          break;
        case 2:
          display2.print("Freestyle");
          break;
        case 3:
          display2.print("Trot");
          break;
        case 4:
        display2.print("Options");
        break;
      }
      display2.setCursor(0, 20);
      display2.setTextSize(1);
      display2.print("SELECTED!");
      display2.display();
      cur_rgb_val1[0] = 255; cur_rgb_val1[1] = 0; cur_rgb_val1[2] = 0;
      cur_rgb_val2[0] = 0; cur_rgb_val2[1] = 0; cur_rgb_val2[2] = 0;
      rgb_num = 99;
      pattern = 9;
      pattern_cnt = 1;
      pattern_int = 10;
      }
    }
  }
}


void check_joysticks() {
  byte rjxcen = 127;
  byte rjycen = 127;
  byte ljxcen = 127;
  byte ljycen = 127;

  int rjx = map(analogRead(RJX_PIN), rj_min, rj_max, j_min, j_max);
  if (rjx != tm_data[12]) {
    if (rjx < jstick_center[1] && rjx > -jstick_center[1]) {
      rjx = 0;
    }
    //    inactivity_set = 0;
    tm_data[12] = rjx;

    if (debug4) {
      if (!rjx && (!set_led[1] || !set_led[3])) {
        led_strip.setPixelColor(1, led_strip.Color(0, 0, 0));
        led_strip.setPixelColor(3, led_strip.Color(0, 0, 0));
        set_led[1] = 0;
        set_led[3] = 0;
      } else if (rjx > jstick_center[0]) {
        set_led[3] = 1;
        led_strip.setPixelColor(3, led_strip.Color(0, 0, 255));
      } else if (rjx < -jstick_center[0]) {
        set_led[1] = 1;
        led_strip.setPixelColor(1, led_strip.Color(0, 0, 255));
      }
    }
  }

  int ljx = map(analogRead(LJX_PIN), lj_min, lj_max, j_min, j_max);
  if (ljx != tm_data[10]) {
    if (ljx < jstick_center[1] && ljx > -jstick_center[1]) {
      ljx = 0;
    }
//    inactivity_set = 0;
    tm_data[10] = ljx;

    if (debug4) {
      if (!ljx && (!set_led[1] || !set_led[3])) {
        led_strip.setPixelColor(1, led_strip.Color(0, 0, 0));
        led_strip.setPixelColor(3, led_strip.Color(0, 0, 0));
        set_led[1] = 0;
        set_led[3] = 0;
      } else if (ljx > jstick_center[0]) {
        set_led[3] = 1;
        led_strip.setPixelColor(3, led_strip.Color(0, 0, 255));
      } else if (ljx < -jstick_center[0]) {
        set_led[1] = 1;
        led_strip.setPixelColor(1, led_strip.Color(0, 0, 255));
      }
      led_strip.show();
    }
  }

  int rjy = map(analogRead(RJY_PIN), rj_min, rj_max, j_max, j_min);
  if (rjy != tm_data[13]) {
    if (rjy < jstick_center[1] && rjy > -jstick_center[1]) {
      rjy = 0;
    }
//    inactivity_set = 0;
    tm_data[13] = rjy;

    if (debug4) {
      if (!rjy && (!set_led[0] || !set_led[4])) {
        led_strip.setPixelColor(0, led_strip.Color(0, 0, 0));
        led_strip.setPixelColor(4, led_strip.Color(0, 0, 0));
        set_led[0] = 0;
        set_led[4] = 0;
      } else if (rjy > jstick_center[1]) {
        set_led[0] = 1;
        led_strip.setPixelColor(0, led_strip.Color(0, 255, 0));
      } else if (rjy < -jstick_center[1]) {
        set_led[4] = 1;
        led_strip.setPixelColor(4, led_strip.Color(0, 255, 0));
      }
    }
  }

  int ljy = map(analogRead(LJY_PIN), lj_min, lj_max, j_max, j_min);
  if (ljy != tm_data[11]) {
    if (ljy < jstick_center[1] && ljy > -jstick_center[1]) {
      ljy = 0;
    }
//    inactivity_set = 0;
    tm_data[11] = ljy;

    if (debug4) {
      if (!ljy && (!set_led[0] || !set_led[4])) {
        led_strip.setPixelColor(0, led_strip.Color(0, 0, 0));
        led_strip.setPixelColor(4, led_strip.Color(0, 0, 0));
        set_led[0] = 0;
        set_led[4] = 0;
      } else if (ljy > jstick_center[1]) {
        set_led[0] = 1;
        led_strip.setPixelColor(0, led_strip.Color(0, 255, 0));
      } else if (ljy < -jstick_center[1]) {
        set_led[4] = 1;
        led_strip.setPixelColor(4, led_strip.Color(0, 255, 0));
      }
      led_strip.show();
    }
  }

  controlsUpdate = millis();

  if (debug4) {
    display.clearDisplay();
    display.setTextSize(2);
    display.setCursor(10,18);
    display.print(ljx);
    display.print(",");
    display.println(ljy);
    display.setCursor(10,47);
    display.print(rjx);
    display.print(",");
    display.println(rjy);
  }
}

void check_mode(){
  tm_data[14] = selected_mode;
}

/*
   -------------------------------------------------------
   OLED Functions
   -------------------------------------------------------
*/
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

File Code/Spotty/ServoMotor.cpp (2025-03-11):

#include <string.h>
#include "ServoMotor.h"
#include "globals.h"

ServoMotor::ServoMotor()
{
	mId = -1;
	mTargetDegree = -1;
	mCurrentDegree = -1;
	mIsMoving = false;
  mReverse = false;
  mName = NULL;
}

ServoMotor::~ServoMotor()
{
  if (mName)
    delete []mName;
}

void ServoMotor::update(unsigned long mills)
{
  if (mId < 0)
    return;

	if (mIsMoving)
	{
		if (mills >= mEndTime) //End of movement is reached: Write the target angle to the motor and set moving variable to false
		{

			write_degree(mTargetDegree);
			mIsMoving = false;
		}
		else //Time is smaller than end time which means that the movement is still performing
		{
      if (mTargetDegree == mCurrentDegree) //If Target is reached return
        return;
    
      double perc = (double)(mills - mStartTime) / (double)(mEndTime - mStartTime);

		  double pos_degree;

      if (mRamp > 0.0)
      {
				double velocitymax = (mTargetDegree - mStartDegree) / (1.0 - mRamp);

				double velocity;

        if (perc < mRamp) // ramp UP
				{
					velocity = perc / mRamp *  velocitymax;

					pos_degree = mStartDegree + perc * velocity / 2.0;

				}
				else if (perc < (1.0 - mRamp)) // constant velocity
				{
					velocity = velocitymax;

					pos_degree = mStartDegree + (mRamp / 2.0 + perc - mRamp) * velocitymax;

				}
				else // ramp DOWN
				{
					velocity = (1.0 - perc) / mRamp * velocitymax;

					pos_degree = mStartDegree + (1.0 - mRamp) * velocitymax - velocity * (1.0 - perc) / 2;

				}
      }
      else // No ramp
      {
		    pos_degree = mStartDegree + (mTargetDegree - mStartDegree) * perc;
        
      }
			write_degree(pos_degree);
		}
	}
}

void ServoMotor::write_degree(double degree)
{
	  if (mId < 0)
			return;

      // Instead of adding mCorrection (in degrees), use the pulse correction as in moveToAngle.
  // First, ensure the degree is within bounds:
  degree = CutOffDegrees(degree);
  
  // Calculate the corrected pulse using the same method as in moveToAngle:
  int value_in_pulse = angle_to_pulse(degree, mReverse) - mCorrectionPulse;
  
  // Update mCurrentDegree (using the non-corrected angle):
  mCurrentDegree = degree;
  if (value_in_pulse != mCurrentPulse) // Only write if there's a change
  {
    pwm.writeMicroseconds(mId, value_in_pulse);
    mCurrentPulse = value_in_pulse;
  }
}

void ServoMotor::Attach(int id, double correction)
{
	mId = id;
	//mHome = ; //Calculate this
  mCorrection = correction;
  mDegreeRange = SERVO_DEGREERANGE;
  mCorrectionPulse = correctionValues[id];

}

void ServoMotor::setName(const char * owner, const char * name)
{
  mName = new char[strlen(owner) + strlen(name) + 2];
  
  sprintf(mName, "%s-%s", owner, name);
}

void ServoMotor::moveToAngle(double angle)
{
  //Check reverse

  angle = CutOffDegrees(angle); //Checks if angle is inside bounds
  double microseconds = angle_to_pulse(angle, mReverse) - mCorrectionPulse;
  mCurrentDegree = angle;
  mCurrentPulse = microseconds;
	pwm.writeMicroseconds(mId, microseconds);

}

void ServoMotor::printAllServoValues() {
    Serial.println("########################################");
    Serial.print("VALUES FOR: ");
    Serial.println(getName());
    Serial.print("Id: ");
    Serial.println(getId());
    Serial.print("IsMoving: ");
    Serial.println(getIsMoving());
    Serial.print("ReverseValue: ");
    Serial.println(getReverse());
    Serial.print("CenterPulse: ");
    Serial.println(getCenterPulse());
    Serial.print("CurrentPulse: ");
    Serial.println(getCurrentPulse());
    Serial.print("DegreeRange: ");
    Serial.println(getDegreeRange());
    Serial.print("Correction: ");
    Serial.println(getCorrection());
    Serial.print("CorrectionPulse: ");
    Serial.println(getCorrectionPulse());
    Serial.print("Home: ");
    Serial.println(getHome());
    Serial.print("CurrentDegree: ");
    Serial.println(getCurrentDegree());
    Serial.print("TargetDegree: ");
    Serial.println(getTargetDegree());
    Serial.print("StartDegree: ");
    Serial.println(getStartDegree());
    Serial.print("Ramp: ");
    Serial.println(getRamp());
    Serial.print("StartTime: ");
    Serial.println(getStartTime());
    Serial.print("EndTime: ");
    Serial.println(getEndTime());
    Serial.print("Min: ");
    Serial.println(getMin());
    Serial.print("Max: ");
    Serial.println(getMax());
    Serial.println("########################################");
}

void ServoMotor::setCenterPulse(double centerPulse){
  mCenterPulse = centerPulse;
}

void ServoMotor::StartMovement(unsigned long mills, double degree, unsigned long duration, double ramp)
{
	degree = CutOffDegrees(degree);
  ramp = CutOffRamp(ramp);

  mTargetDegree = degree;
  mStartDegree = mCurrentDegree;
  mStartTime = mills;
  mEndTime = mStartTime + duration;
  mRamp = ramp;

  mIsMoving = true;
}

void ServoMotor::SetLimits(double low, double high)
{
	  mLimitLow = low;
		if (mLimitLow < 0.0)
			mLimitLow = 0.0;

		mLimitHigh = high;
		if (mLimitHigh > mDegreeRange)
			mLimitHigh = mDegreeRange;
}

double ServoMotor::CutOffDegrees(double degree)
{
	if (degree < mLimitLow)
		return mLimitLow;
	else if (degree > mLimitHigh)
		return mLimitHigh;
  return degree;
}

double ServoMotor::CutOffRamp(double ramp)
{
  if (ramp < 0)
    return 0;
  if (ramp > 0.4)
    return 0.4;
  return ramp;
}

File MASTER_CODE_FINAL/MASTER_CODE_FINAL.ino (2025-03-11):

#include <Wire.h>
#include "globals.h"
#include "functions.h"
#include "MyBody.h"
#include "MyLeg.h"
#include "ServoMotor.h"
MyBody robot;


void setup() {
  //Initialize all components
  //init_serial();
  init_servos();
  init_MP3();
  init_NRF24();
  init_MagnetSensor();
  check_Remote();
  // Load neutral positions from EEPROM and write them to the robot and then take neutral Position
  loadNeutralPositions_EEPROM();
  //Calc Correction Values
  calculateCorrectionValues();

  //Attach servos and set Values
  robot.mRightFront.mTibia.Attach(0, deltaPulse_to_deltaAngle(correctionValues[0]));    //FRONT-RIGHT
  robot.mRightFront.mTibia.setCenterPulse(neutralPositions[0]);
  robot.mRightFront.mTibia.SetLimits(120.0, 320.0);
  robot.mRightFront.mFemur.Attach(1, deltaPulse_to_deltaAngle(correctionValues[1]));
  robot.mRightFront.mFemur.setCenterPulse(neutralPositions[1]);
  robot.mRightFront.mFemur.SetLimits(110.0, 260.0);
  robot.mRightFront.mCoax.Attach(2, deltaPulse_to_deltaAngle(correctionValues[2]));
  robot.mRightFront.mCoax.setCenterPulse(neutralPositions[2]);
  robot.mRightFront.mCoax.SetLimits(150.0, 210.0);

  robot.mLeftFront.mTibia.Attach(3, deltaPulse_to_deltaAngle(correctionValues[3]));     //FRONT-LEFT
  robot.mLeftFront.mTibia.setCenterPulse(neutralPositions[3]);
  robot.mLeftFront.mTibia.SetLimits(120.0, 320.0);
  robot.mLeftFront.mFemur.Attach(4, deltaPulse_to_deltaAngle(correctionValues[4]));
  robot.mLeftFront.mFemur.setCenterPulse(neutralPositions[4]);
  robot.mLeftFront.mFemur.SetLimits(110.0, 260.0);
  robot.mLeftFront.mCoax.Attach(5, deltaPulse_to_deltaAngle(correctionValues[5]));
  robot.mLeftFront.mCoax.setCenterPulse(neutralPositions[5]);
  robot.mLeftFront.mCoax.SetLimits(150.0, 210.0);

  robot.mRightRear.mTibia.Attach(6, deltaPulse_to_deltaAngle(correctionValues[6]));     //REAR-RIGHT
  robot.mRightRear.mTibia.setCenterPulse(neutralPositions[6]);
  robot.mRightRear.mTibia.SetLimits(120.0, 320.0);
  robot.mRightRear.mFemur.Attach(7, deltaPulse_to_deltaAngle(correctionValues[7]));
  robot.mRightRear.mFemur.setCenterPulse(neutralPositions[7]);
  robot.mRightRear.mFemur.SetLimits(110.0, 260.0);
  robot.mRightRear.mCoax.Attach(8, deltaPulse_to_deltaAngle(correctionValues[8]));
  robot.mRightRear.mCoax.setCenterPulse(neutralPositions[8]);
  robot.mRightRear.mCoax.SetLimits(150.0, 210.0);

  robot.mLeftRear.mTibia.Attach(9, deltaPulse_to_deltaAngle(correctionValues[9]));     //REAR_LEFT
  robot.mLeftRear.mTibia.setCenterPulse(neutralPositions[9]);
  robot.mLeftRear.mTibia.SetLimits(120.0, 320.0);
  robot.mLeftRear.mFemur.Attach(10, deltaPulse_to_deltaAngle(correctionValues[10]));
  robot.mLeftRear.mFemur.setCenterPulse(neutralPositions[10]);
  robot.mLeftRear.mFemur.SetLimits(110.0, 260.0);
  robot.mLeftRear.mCoax.Attach(11, deltaPulse_to_deltaAngle(correctionValues[11]));
  robot.mLeftRear.mCoax.setCenterPulse(neutralPositions[11]);
  robot.mLeftRear.mCoax.SetLimits(150.0, 210.0);

  //Get the robot in the zero state to check if calibration is needed
  robot.goNeutral();
  delay(1000);

  //Log the init state for every Motor
  robot.logState();

  //Ask User to enter Calibration-Setup  #### Uncomment this for PC Serial Use
  //bool calibrationCheck = askUserForCalibration();
  //if (calibrationCheck) {
    //startCalibration();
  //}

  //Play Sniffing sound to end setup
  myDFPlayer.play(5);

  //wait for remote to be connected
  delay(2000);
}


void loop() {
  static unsigned int last_mills = 0;
  unsigned long now_mills = millis();
  robot.setGait(GAIT_TROT); // select WALK mode

  if (last_mills != now_mills)
  {
    last_mills = now_mills;

    if (radio.available()) {
      check_Remote();
      get_remote_data();  //Gets Data from Remote and also sends Robot Data back to the Remote
      get_joystick_commands();
    }
    //Serial.print("CurrentPos: ");
    //Serial.println(currentPosition);

    if(currentPosition == "forward"){
      robot.StartWalk(600);
    }

    else if(currentPosition == "backwards"){
      robot.StartWalk(600);
    }

    else if(currentPosition == "right"){
      robot.StartWalk(600);
      robot.WalkTurn(TURN_RIGHT);
    }

    else if(currentPosition == "left"){
      robot.StartWalk(600);
      robot.WalkTurn(TURN_LEFT);
    }

    else if(currentPosition == "middle"){
      robot.StopWalk(now_mills);
    }
    // Execute asynch servo movements
    robot.update(now_mills);
    check_magnetic_field();
  }

    
}

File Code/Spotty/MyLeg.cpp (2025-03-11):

#include "MyLeg.h"
#include "globals.h"

#define square(x) x*x

MyLeg::MyLeg(bool left, bool front)
{
  mFront = front;
  mLeft = left;
}

void MyLeg::setName(const char * name) 
{
  mName = new char[strlen(name) + 1];
  strcpy(mName, name);

  mTibia.setName(mName,"Tibia");
  mFemur.setName(mName,"Femur");
  mCoax.setName(mName,"Coax");
}

void MyLeg::setReverse(bool value)
{
  mTibia.setReverse(value);
  mFemur.setReverse(value);
  mCoax.setReverse(value);
}

//------------PUBLIC FUNCTIONS-------------------

void MyLeg::update(unsigned long mills)
{
  mTibia.update(mills);
  mFemur.update(mills);
  mCoax.update(mills);
}

void MyLeg::DoStep(unsigned long mills, double percentage, unsigned long duration, unsigned long turning)
{
  coords delta = StepCurve(percentage, turning);
  
  GoPosition(mills, delta, duration);
}


void MyLeg::neutral() {
  mTibia.moveToAngle(SERVO_DEGREERANGE/2);
  mFemur.moveToAngle(SERVO_DEGREERANGE/2);
  mCoax.moveToAngle(SERVO_DEGREERANGE/2);
}

void MyLeg::logState(){
  mTibia.printAllServoValues();
  mFemur.printAllServoValues();
  mCoax.printAllServoValues();
}

void MyLeg::GoPosition(unsigned long mills, double x, double y, double z, unsigned long duration, double ramp)
{
  angle a = IKSolver(x, y, z);

  mPosition.x = x;
  mPosition.y = y;
  mPosition.z = z;


  mTibia.StartMovement(mills, a.tibia_degree, duration, ramp);
  mFemur.StartMovement(mills, a.femur_degree, duration, ramp);
  mCoax.StartMovement(mills, a.coax_degree, duration, ramp); 
}

void MyLeg::GoPosition(unsigned long mills, coords delta, unsigned long duration, double ramp)
{
  double new_x = mPosition.x + delta.x;
  double new_y = mPosition.y + delta.y;
  double new_z = mPosition.z + delta.z;
  
  angle a = IKSolver(new_x, new_y, new_z);

  mTibia.StartMovement(mills, a.tibia_degree, duration);
  mFemur.StartMovement(mills, a.femur_degree, duration);
  mCoax.StartMovement(mills, a.coax_degree, duration); 
}

//------------PRIVATE FUNCTIONS-------------------
angle MyLeg::IKSolver(double x, double y, double z)
{
  z = z + COAX_SIZE;

  double d1 = sqrt(square(z) + square(y) - square(COAX_SIZE));
  double d2 = sqrt(square(d1) + square(x));
  double d3 = (square(d2) - square(FEMUR_SIZE) - square(TIBIA_SIZE)) / (2 * FEMUR_SIZE * TIBIA_SIZE);

  double theta1 = -atan2(y, z) - atan2(d1, -COAX_SIZE);
  double theta3 = acos(d3);
  double theta2 = atan2(x,d1) - atan2(TIBIA_SIZE * sin(theta3), FEMUR_SIZE + TIBIA_SIZE * cos(theta3));

  angle a;

  theta1 = theta1 + (2*M_PI);
  theta2 = theta2 + M_PI;
  theta3 = theta3 + M_PI;

  if (theta1 >= 0)
    a.coax_degree  = 180.0 * theta1 / M_PI;
  else
    a.coax_degree  = 180 + 180.0 * theta1 / M_PI;

  if (theta2 >= 0)
    a.femur_degree  =  180.0 * theta2 / M_PI;
  else
    a.femur_degree  = 180 + 180.0 * theta2 / M_PI;

  if (theta3 >= 0)
    a.tibia_degree  = 180.0 * theta3 / M_PI;
  else
    a.tibia_degree  = 180 + 180.0 * theta3 / M_PI;

  return a;
}
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

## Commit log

2025-01-08 First Working Remote Version
    Sends the following Data via NRF on Channel 124:
    - 4 Fire Buttons (Momentary Switch)
    - 2 Select Buttions (Momentary Switch)
    - 4 Slide Potentiometers
    - 2 Joysticks with their X and Y Value
2025-02-12 Added magnetic sensor and MP3 Plyer
    Make sure to change compass library!
2025-03-01 Changed to a OOP Based Approach
    - Added Body Class
    - Added Leg Class
    - Added ServoMotor Class
    - Added move Function for Leg that accepts 3 angles as inputs
    - Added goNeutral function that loads neutralPositions from EEROM
    - Angle is being corrected by a calibrationValue that is calculated from neutral_pos and stored EEROM Values
    - Angle is being mapped to microseconds in the move function (180 degree is center which is 1550ms)
    [Calibrate.ino, MyLeg.cpp, ServoMotor.cpp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]
2025-03-04 Changed to a new Codebase
    - OOP based approach
    - IK-Model working
    - Can go to walk-position with correct Calibration offsets
    [MASTER_CODE_FINAL.ino, MyLeg.cpp, ServoMotor.cpp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]
2025-03-11 Finished Code for MA
    - Fixed issue with remote connection and cramping of legs
    - can move in 4 directions with remote now
    [MASTER_CODE_FINAL.ino, MyLeg.cpp, ServoMotor.cpp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]
